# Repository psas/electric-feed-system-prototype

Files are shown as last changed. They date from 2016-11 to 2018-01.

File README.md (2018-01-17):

Electric Feed System
======================

Electric feed system (EFS) aims to design, build, and test an electric feed system prototype using COTS parts and in-house manufacturing for the PSAS LV4 liquid fueled bi-propellant rocket engine by June 6, 2017.

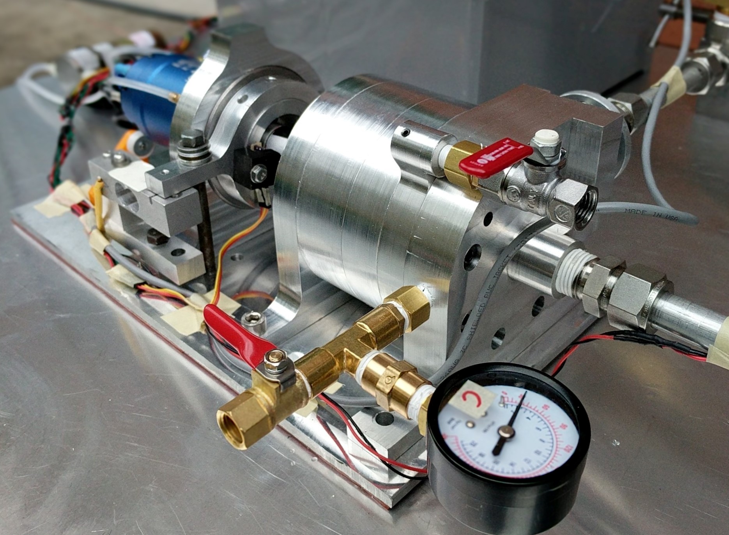
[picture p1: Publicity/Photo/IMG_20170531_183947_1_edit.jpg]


## EFS Requirements:

1. Design and bench test a technology development platform for the electric pump fed system.
2. Design and test a custom power system for EFS motor and system controls.
3. Design for the existing LFE (target chamber pressure of 350 - 400 psi)
4. The pump must be constructed from COTS components.
5. Parallel work with Carbon Fiber Propellant Tank (CFPT) team to optimize vehicle integration.
6. IPython design tool to generate pump requirements based on engine/vehicle level parameters.    
7. Harness the following documentation:
    - EFS testing, handling, and troubleshooting procedures
    - EFS Design Methodology & Design Process
    - Complete bill of materials man

## Stretch Goals:

- Integration with existing Liquid Fuelled Engine Test Stand (LFETS)
- Completed live health monitoring and emergency shutdown provisions
- Cold fire LN2 testing
- Cold fire LOX testing
- Hot  fire LOX testing

### Project Members

Name                | GitHub Username | Current Role
--------------------|-----------------|-----------------------------------
Johnny C. Froehlich | @JordParma      | Team Lead; Design Engineer; Analysis; Testing
James A. Luce       | @luceja         | Mechanical Design Lead; Control Systems
Johnathan Talik     | @jtalik         | Fabrication 
Rawand Rasheed      | @rawand12       | Control Systems
Jordan Roland       | @JSRoland       | Add project role
Mimi Shang          | @mimishang      | Add project role

### Important links

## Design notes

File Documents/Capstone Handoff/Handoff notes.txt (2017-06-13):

Present design:
	Overview of design features
	Individual component analysis
	Subsystems
		Mechanical
		Electrical
		Controls
		Working fluid delivery
	
Design overview questions:

Future work:
	Rework electrical to accomodate more continuous testing
		Power supply?
		Better batteries?
		New motor (custom job?)
	Rework controls for more reliable testing at higher RPM
		Further separation between operators and test stand
		Hide the rats nest somewhere...

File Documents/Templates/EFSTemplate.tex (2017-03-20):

\documentclass[11pt,twoside,a4paper,openright]{report}

\usepackage[utf8]{inputenc}
\usepackage[english]{babel}
\usepackage{lmodern}
\usepackage[T1]{fontenc}
\usepackage{xcolor}
\definecolor{aaublue}{RGB}{33,26,82}
\usepackage{graphicx}
\usepackage{tabularx}
\usepackage{caption}
\captionsetup{%
  font=footnotesize,
  labelfont=bf 
  }
\usepackage{array,booktabs}
\usepackage{wrapfig}
\usepackage{adjustbox}
\usepackage{framed}
\usepackage{amsmath}
\usepackage{amssymb}
\usepackage[framed,amsmath,thmmarks]{ntheorem}
\usepackage{dblfloatfix}
\usepackage{adjustbox}
\usepackage{layouts}

\usepackage[
  left=0.5in,
  right=0.5in,
  bottom=1mm,
  top= 1in,
  ]{geometry}
\usepackage{titlesec}
\titleformat*{\section}{\normalfont\Large\bfseries
    }
\titleformat*{\subsection}{\normalfont\large\bfseries
    }
\titleformat*{\subsubsection}{\normalfont\normalsize\bfseries
    }
%\titleformat*{\paragraph}{\normalfont\normalsize\bfseries}}
%\titleformat*{\subparagraph}{\normalfont\normalsize\bfseries}}

% configure section titles
\usepackage{titlesec}
\titleformat{\section}{\Large\bfseries}{\thesection}{1em}{}
\titleformat{\subsection}{\large\bfseries}{\thesubsection}{1em}{}

\begin{document}
% custom commands
\newcommand{\windef}[1]{\subsection*{\underline{DEF:} \normalsize{#1}}} % definition
\newcommand{\winex}[1]{\subsection*{\underline{EX:} \normalsize{#1}}} % example
\newcommand{\winsec}[1]{\section*{\underline{\textbf{#1}}}} % section
\newcommand{\winres}[1]{\begin{math}\Rightarrow\left\{\begin{matrix}#1\end{matrix}\right.\end{math}\hspace{0.2cm}} % result
\newcommand{\winsys}[1]{\begin{math}\left\{\begin{matrix}#1\end{matrix}\right.\end{math}} % system
\newcommand{\winero}[1]{\begin{math}\xrightarrow{#1}\end{math}} % row operation
\newcommand{\winmat}[1]{\begin{math}\begin{bmatrix}#1\end{bmatrix}\end{math}} % matrix
\newcommand{\winsub}[1]{\subsection*{$\star$\hspace{0.2cm} #1}} % dot
\newcommand{\step}[1]{\begin{math}\xrightarrow{\text{#1}}\end{math}} % step in a process
\newcommand{\winrtwo}{\begin{math}\text{R}^\text{2}\end{math}}
\newcommand{\winrthree}{\begin{math}\text{R}^\text{3}\end{math}}
\newcommand{\wineq}[1]{\begin{equation}\notag#1\end{equation}}
\newcommand{\winans}[1]{\begin{equation}\underline{\underline{\notag\boldsymbol{#1}}}\Leftarrow\end{equation}}
\newcommand{\horrule}[1]{\rule{\linewidth}{#1}} % Create horizontal rule command with 1 argument of height

\begin{titlepage}

\vfil
	\centering
	{\huge\bfseries PSAS Liquid Propellant Rocket Engine
Electric Feed System\par}
	\vspace{0.5cm}
	{\scshape\Large Conceptual Design Progress Report\par}% Insert Document title here

\vspace{2cm}

	{\Large\itshape 	{Jorden Roland, 
John Froehlich,\\
James Luce, 
Mimi Shang,\\
John Talik, 
Rawand Rasheed\par}}

\vspace{3cm}
Faculty advisor:\par
    \textsc{Ra\'{u}l Bayo\'{a}n Cal}\par
	Supervised by:\par
    \textsc{Erin Schmidt}\\
	and\\
	\textsc{Andrew Greenberg}

	\vspace{3cm}
	
%textwidth in cm: \printinunitsof{cm}\prntlen{\textwidth}

\begin{table*}[!t]

  \begin{tabular}{  p{2cm}  m{13.20337cm}  p{2cm}  }
  
\\ \hline

\begin{minipage}{.3\textwidth}
 \begin{flushleft}
      
 \end{flushleft}
\end{minipage}

&

\begin{center}
	{Portland State Aerospace Society}\par
	{Fariborz Maseeh College of Engineering and Computer Science}\par
	{\large \today \par}
	\end{center}

&	

\begin{minipage}{.3\textwidth}
%\begin{flushright}
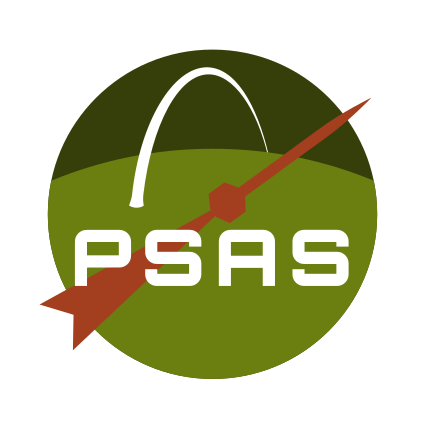
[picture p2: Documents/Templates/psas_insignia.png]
      
%      \end{flushright}
    \end{minipage}\\ \hline
   
\end{tabular}
\end{table*}

\end{titlepage}
\newgeometry{top=10mm,bottom=10mm,right=15mm,left=15mm}
\newpage

\winsec{Nomenclature:}

\centering{
\begin{tabularx}{1.5\textwidth}{c c c c}\par
\textbf{Symbol:} & \textbf{Name:} & \textbf{Formula:} & \textbf{Dependecies:}\par
\end{tabularx}\par
}

\winsec{Abstract:}   %comment out this line and the next if there is no abstract!!!

\newpage
\winsec{Introduction:}
\winsec{Model:}
\winsec{Results:}
\winsec{Conclusion:}
\winsec{Acknowledgments:}
\winsec{References:}

\end{document}

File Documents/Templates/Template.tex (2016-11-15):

\documentclass[12pt]{article}
\usepackage[T1]{fontenc}
\usepackage{graphicx}
\usepackage[font=small]{caption}
\usepackage{amsmath,amssymb,amsfonts,amsthm}
\usepackage{eso-pic}
\usepackage{lastpage}
\usepackage[left=2.7cm,right=1.7cm,top=1.65cm,bottom=1.0cm]{geometry}

\usepackage{fontspec}

\usepackage{tkz-euclide}
\usepackage{multicol}
\usepackage{pgfplots}
\pgfplotsset{compat=1.8}
\usepackage{pgfplotstable}
\usepackage{tikz}
\usetkzobj{all}
\usepackage{booktabs}
\usepackage{listings}
\usepackage{stmaryrd}
%\usepackage{courier}
%\setmonofont{Courier New}
\lstset{
language=R,
basicstyle=\scriptsize\ttfamily,
commentstyle=\ttfamily\color{gray},
numbers=left,
numberstyle=\ttfamily\color{gray}\footnotesize,
stepnumber=1,
numbersep=5pt,
backgroundcolor=\color{white},
showspaces=false,
showstringspaces=false,
showtabs=false,
frame=single,
tabsize=2,
captionpos=b,
breaklines=true,
breakatwhitespace=false,
title=\lstname,
escapeinside={},
keywordstyle={},
morekeywords={},
morecomment=[l][\color{red}]{>\ }
}

% configure page header
\usepackage{fancyhdr}
\setlength{\headheight}{18pt}
\pagestyle{fancy}\fancyhf{}
\renewcommand{\headrulewidth}{0pt}
\renewcommand{\footrulewidth}{0pt}
\lhead{\large{11/3/16}}
\chead{\large{ME 488 - HWK \#004}\hspace{1.4cm}}
\rhead{\large{\MakeUppercase{JORDEN ROLAND}}\hspace{1.5cm}\thepage\hspace{0.1cm}/\hspace{0.1cm}\pageref{LastPage}\hspace{-1.5cm}}

% background image
\newcommand\BackgroundPic{
\put(0,0){
\parbox[b][\paperheight]{\paperwidth}{%
\vfill
\centering
%
\vfill
}}}

% configure section titles
\usepackage{titlesec}
\titleformat{\section}{\Large\bfseries}{\thesection}{1em}{}
\titleformat{\subsection}{\large\bfseries}{\thesubsection}{1em}{}

\begin{document}

\AddToShipoutPicture{\BackgroundPic}

% custom commands
\newcommand{\windef}[1]{\subsection*{\underline{DEF:} \normalsize{#1}}} % definition
\newcommand{\winex}[1]{\subsection*{\underline{EX:} \normalsize{#1}}} % example
\newcommand{\winsec}[1]{\section*{\underline{#1}}} % section
\newcommand{\winres}[1]{\begin{math}\Rightarrow\left\{\begin{matrix}#1\end{matrix}\right.\end{math}\hspace{0.2cm}} % result
\newcommand{\winsys}[1]{\begin{math}\left\{\begin{matrix}#1\end{matrix}\right.\end{math}} % system
\newcommand{\winero}[1]{\begin{math}\xrightarrow{#1}\end{math}} % row operation
\newcommand{\winmat}[1]{\begin{math}\begin{bmatrix}#1\end{bmatrix}\end{math}} % matrix
\newcommand{\winsub}[1]{\subsection*{$\star$\hspace{0.2cm} #1}} % dot
\newcommand{\step}[1]{\begin{math}\xrightarrow{\text{#1}}\end{math}} % step in a process
\newcommand{\winrtwo}{\begin{math}\text{R}^\text{2}\end{math}}
\newcommand{\winrthree}{\begin{math}\text{R}^\text{3}\end{math}}
\newcommand{\wineq}[1]{\begin{equation}\notag#1\end{equation}}
\newcommand{\winans}[1]{\begin{equation}\underline{\underline{\notag\boldsymbol{#1}}}\Leftarrow\end{equation}}
%%%%%%%%%%%%%%%%%%%%%%
% start writing here %
%%%%%%%%%%%%%%%%%%%%%%
\winsec{Question 1: Fractional Factorials}

\winsub{Given}

\begin{enumerate}
  \item $2^{5-2}$
  \item $2^{8-4}$
  \item $2^6$
\end{enumerate}

\winsub{Find}

Runs per replicate needed for each of the above Fractional Factorials

\winsub{Solution}

\begin{enumerate}
  \item $2^{5-2} = 2^3 = 8$ runs per replicate.
  \item $2^{8-4} = 2^4 = 16$ runs per replicate.
  \item $2^6 = 64$ runs per replicate.
\end{enumerate}

\vspace{0.5in}
\noindent\hfil\rule{0.5\textwidth}{.8pt}\hfil

\winsec{Question 2: Use R to Generate Fractional Factorials}

\winsub{Given}

\begin{enumerate}
  \item Any $2^{5-1}$
  \item A $2^{8-3}$ with the generators F=ABC, G=ABD, H=BCD
\end{enumerate}

\winsub{Find}

Use R and the FrF2 Package to create the above and display the +1/-1 matrices

\newpage

\winsub{Solution}
\begin{enumerate}
\item \hspace{1.0cm}\begin{lstlisting}
> library(DoE.base)
> library(FrF2)
> FrF2(2^4,5)
    A  B  C  D  E
1  -1  1  1  1 -1
2   1  1 -1 -1  1
3  -1  1 -1  1  1
4  -1 -1  1  1  1
5   1 -1  1 -1  1
6   1  1  1  1  1
7   1 -1  1  1 -1
8  -1  1 -1 -1 -1
9   1  1 -1  1 -1
10 -1 -1 -1 -1  1
11 -1 -1  1 -1 -1
12  1  1  1 -1 -1
13  1 -1 -1 -1 -1
14 -1 -1 -1  1 -1
15 -1  1  1 -1  1
16  1 -1 -1  1  1
class=design, type= FrF2 
\end{lstlisting}
\item  \hspace{1.0cm}\begin{lstlisting}
> FrF2(2^5,8,generator=c("ABC","ABD","BCD"))
    A  B  C  D  E  F  G  H
1   1 -1 -1  1  1  1 -1  1
2  -1 -1 -1  1  1 -1  1  1
3  -1  1  1  1 -1 -1 -1  1
4   1  1  1  1  1  1  1  1
5  -1 -1  1  1  1  1  1 -1
6   1  1 -1  1  1 -1  1 -1
7   1 -1  1  1  1 -1 -1 -1
8  -1 -1  1 -1  1  1 -1  1
9  -1  1 -1  1 -1  1 -1 -1
10 -1  1  1 -1  1 -1  1 -1
11  1 -1  1 -1  1 -1  1  1
12 -1  1 -1 -1  1  1  1  1
13  1 -1 -1 -1  1  1  1 -1
14  1  1 -1  1 -1 -1  1 -1
15 -1  1 -1 -1 -1  1  1  1
16 -1 -1 -1  1 -1 -1  1  1
17 -1  1  1  1  1 -1 -1  1
18 -1 -1 -1 -1  1 -1 -1 -1
19  1 -1 -1  1 -1  1 -1  1
20  1 -1 -1 -1 -1  1  1 -1
21  1 -1  1 -1 -1 -1  1  1
22  1  1 -1 -1  1 -1 -1  1
23  1  1  1  1 -1  1  1  1
24 -1 -1  1 -1 -1  1 -1  1
25  1  1  1 -1 -1  1 -1 -1
26 -1  1  1 -1 -1 -1  1 -1
27  1 -1  1  1 -1 -1 -1 -1
28 -1 -1 -1 -1 -1 -1 -1 -1
29 -1 -1  1  1 -1  1  1 -1
30  1  1 -1 -1 -1 -1 -1  1
31 -1  1 -1  1  1  1 -1 -1
32  1  1  1 -1  1  1 -1 -1
class=design, type= FrF2.generators
\end{lstlisting}
\end{enumerate}

\newpage

\winsec{Question 3: Aliasing}

\winsub{Given}

\begin{enumerate}
  \item I=ABCD=EBCD=AE
  \item I=ABCDE
\end{enumerate}

\winsub{Find}

The aliases of 'BC' in each of the above

\winsub{Solution}

\begin{enumerate}
  \item Multiply through the defining words by `BC' gives its aliases.\\
  (BC)I=(BC)ABCD=(BC)EBCD=(BC)AE $\shortrightarrow$  BC=AD=ED=ABCE
  \item Repeat step above.\\
  (BC)I=(BC)ABCDE $\shortrightarrow$ BC=ADE
  \end{enumerate}

\vspace{0.5in}
\noindent\hfil\rule{0.5\textwidth}{.8pt}\hfil

\winsec{Question 4: Resolution}

\winsub{Find}

Explain why a $R_{II}$ fractional experiment is a bad idea? Use an example to illustrate your point.

\winsub{Solution}
In general a $R_{II}$ fractional experiment is not particularly useful because main effects will be confounded with other main effects making it unclear which of the factors is causing a change in the resonse.\\

EX: The simplest case is a $2^{2-1}$ experiment with defining relationship I=AB. In this case A=B and B=A making the two factors being tested completely indistiguishable from each other.

\newpage

\winsec{Question 5: Concepts of Half Fractional}

\winsub{Given}

$2^{4-1}$ Half Fractional Factorial Experiment with the D=ABC generator

\winsub{Find}

The process to create the 'other' half. Hint: D=ABC means D=+ABC

\winsub{Solution}
Generating the ``other half'' of the experiment simply requires setting D=-ABC as below.
\begin{lstlisting}
> FrF2(2^3,4,generator=c("-ABC"))
   A  B  C  D
1  1  1  1 -1
2 -1  1  1  1
3 -1 -1 -1  1
4  1 -1  1  1
5  1 -1 -1 -1
6  1  1 -1  1
7 -1 -1  1 -1
8 -1  1 -1 -1
class=design, type= FrF2.generators 
\end{lstlisting}

\newpage
\winsec{Question 6: Application}

\winsub{Given}

You have been given authorization to study a flame-resistant material. There are 8 key factors, (A,B,C,D,E,F,G,H)

\winsub{Find}

\begin{enumerate}
  \item How many samples at a minimum would you need to request to perform a Full Fractional Experiment of any use?
  \item You have been authorized only 100 samples at maximum. What are the feasible Balanced Fractional Experiments you could run?
  \item For each of the experiments you listed in the last part, what are the engineering trade-offs in the feasible ones?
  \item Pick your choice of experiment and state issues with that experiment you would need to keep in consideration during the analysis phase.
  \item Assume DE and BC are significant and critical two way interactions, use the FrF2 package to determine generators for your choice above to address these.
\end{enumerate}

\winsub{Solution}

\begin{enumerate}
  \item $2^8=256$ runs per replicate. Assuming at \textbf{least} 2 runs for a reasonable number of $df_{error}$ gives $256*2=512$ samples.
  
  \item \textbf{Half-fractional:}	$2^{8-1}=128$ still too many samples.\\
  \textbf{Quarter-fractional:}   $2^{8-2}=64$ This is a pretty good option. ($R_{V}$) and less than 100 samples.\\
  \textbf{Eighth-fractional:} $2^{8-3}=32$ This is probably a low number of samples but not a terrible option ($R_{IV}$). Also leaves enough room to run a second and third replicate which is never bad.\\
  \textbf{Sixteenth-fractional:} $2^{8-4}=16$ Still $R_{IV}$  so this is not a bad option really, allows for oportunity to run multiple replicates. However there may be significant 2-way interactions which are aliased.
  
  \item See above.
  \item Choosing the Eighth-fractional design gives the best options for aliasing combined with the above stated 3 replicates within the funding allowance means that this is likely the best design.
  
  \newpage

  \item Using the FrF2 function in R with the following generators: F=ABC, G=ABD, H=BCDE
  \begin{lstlisting}
  > design.info(FrF2(2^5,8,generator=c("ABC","ABD","BCDE")))$aliased
$legend
[1] "A=A" "B=B" "C=C" "D=D" "E=E" "F=F" "G=G" "H=H"
$main
character(0)
$fi2
[1] "AB=CF=DG" "AC=BF"    "AD=BG"    "AF=BC"    "AG=BD"    "CD=FG"    "CG=DF" 
  \end{lstlisting}
  As shown above DE and BC are not aliased with other interactions and mains are not confounded. this is a solid design.
  
\end{enumerate}

\noindent\hfil\rule{0.5\textwidth}{.8pt}\hfil
\begin{center}
  \textbf{END OF ASSIGNMENT}
\end{center}
\end{document}

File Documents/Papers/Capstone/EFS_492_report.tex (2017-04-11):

\documentclass[11pt,twoside,a4paper,openright]{report}

\usepackage[utf8]{inputenc}
\usepackage[english]{babel}
\usepackage{lmodern}
\usepackage[T1]{fontenc}
\usepackage[table]{xcolor}
\definecolor{aaublue}{RGB}{33,26,82}
\usepackage{graphicx}
\usepackage{tabularx}
\usepackage{caption}
\captionsetup{%
  font=footnotesize,
  labelfont=bf 
  }
\usepackage{array,booktabs}
\usepackage{wrapfig}
\usepackage{adjustbox}
\usepackage{framed}
\usepackage{amsmath}
\usepackage{amssymb}
\usepackage[framed,amsmath,thmmarks]{ntheorem}
\usepackage{dblfloatfix}
\usepackage{adjustbox}
\usepackage{layouts}
\usepackage{lipsum}
\usepackage{pdfpages}
\usepackage{verbatim}
\usepackage{rotating}

\usepackage[
  left=0.5in,
  right=0.5in,
  bottom=1mm,
  top= 1in,
  ]{geometry}
\usepackage{titlesec}
\titleformat*{\section}{\normalfont\Large\bfseries
    }
\titleformat*{\subsection}{\normalfont\large\bfseries
    }
\titleformat*{\subsubsection}{\normalfont\normalsize\bfseries
    }
%\titleformat*{\paragraph}{\normalfont\normalsize\bfseries}}
%\titleformat*{\subparagraph}{\normalfont\normalsize\bfseries}}

% configure section titles
\usepackage{titlesec}
\titleformat{\section}{\Large\bfseries}{\thesection}{1em}{}
\titleformat{\subsection}{\large\bfseries}{\thesubsection}{1em}{}

\begin{document}
% custom commands
\newcommand{\windef}[1]{\subsection*{\underline{DEF:} \normalsize{#1}}} % definition
\newcommand{\winex}[1]{\subsection*{\underline{EX:} \normalsize{#1}}} % example
\newcommand{\winsec}[2]{\section*{\underline{\textbf{#1}}{#2}}} % section
\newcommand{\winres}[1]{\begin{math}\Rightarrow\left\{\begin{matrix}#1\end{matrix}\right.\end{math}\hspace{0.2cm}} % result
\newcommand{\winsys}[1]{\begin{math}\left\{\begin{matrix}#1\end{matrix}\right.\end{math}} % system
\newcommand{\winero}[1]{\begin{math}\xrightarrow{#1}\end{math}} % row operation
\newcommand{\winmat}[1]{\begin{math}\begin{bmatrix}#1\end{bmatrix}\end{math}} % matrix
\newcommand{\winsub}[1]{\subsection*{\hspace{0.2cm}\textit{ #1}}} % dot
\newcommand{\step}[1]{\begin{math}\xrightarrow{\text{#1}}\end{math}} % step in a process
\newcommand{\winrtwo}{\begin{math}\text{R}^\text{2}\end{math}}
\newcommand{\winrthree}{\begin{math}\text{R}^\text{3}\end{math}}
\newcommand{\wineq}[1]{\begin{equation}\notag#1\end{equation}}
\newcommand{\winans}[1]{\begin{equation}\underline{\underline{\notag\boldsymbol{#1}}}\Leftarrow\end{equation}}
\newcommand{\horrule}[1]{\rule{\linewidth}{#1}} % Create horizontal rule command with 1 argument of height

\begin{comment}
\begin{titlepage}

\vfil
	\centering
	{\huge\bfseries PSAS Liquid Propellant Rocket Engine
Electric Feed System\par}
	\vspace{0.5cm}
	{\scshape\Large Conceptual Design Progress Report\par}% Insert Document title here

\vspace{5cm}

	{\Large\itshape 	{Jorden Roland, 
John Froehlich,\\
James Luce, 
Mimi Shang,\\
John Talik, 
Rawand Rasheed\par}}

\vspace{3cm}
Faculty advisor:\par
    \textsc{Ra\'{u}l Bayo\'{a}n Cal}\par
	Supervised by:\par
    \textsc{Erin Schmidt}\\
	and\\
	\textsc{Andrew Greenberg}

	\vspace{3cm}
	
%textwidth in cm: \printinunitsof{cm}\prntlen{\textwidth}

\begin{table*}[!t]

  \begin{tabular}{  p{2cm}  m{13.20337cm}  p{2cm}  }
  
\\ \hline

\begin{minipage}{.3\textwidth}
 \begin{flushleft}
      
 \end{flushleft}
\end{minipage}

&

\begin{center}
	{Portland State Aerospace Society}\par
	{Fariborz Maseeh College of Engineering and Computer Science}\par
	{\large \today \par}
	\end{center}

&	

\begin{minipage}{.3\textwidth}
%\begin{flushright}
      
%      \end{flushright}
    \end{minipage}\\ \hline
   
\end{tabular}
\end{table*}

\end{titlepage}
\newgeometry{top=1in,bottom=1in,right=1in,left=1in}
\newpage
\thispagestyle{empty}

\winsec{Executive Summary: }{}
\vspace{12pt}
The Electric Feed System (EFS) team will design, build, and test an electric feed system prototype to serve as a technology development platform for the PSAS LV4 rocket using commercial off the shelf (COTS) parts and in-house manufacturing by June 16, 2017 and for less than \$15,800.\par
\vspace{12pt}
As of the time of this report, the EFS project is developing the first prototype, which will use water as its working fluid, and is transitioning from design to fabrication and testing. The project is currently ahead of the milestone schedule established by the project plan. \par
\vspace{12pt}
Efforts over the last two months have largely focused on pump sizing and impeller design. The critical decision has been made to transition from theory to validation through physical experiment, allowing us to proceed with the first prototype test. Along with pump theory and design, there have been ongoing parallel efforts to complete the other tasks required for the first prototype test, such as development of controls and data acquisition systems, sensor calibration, completion of CAD design, and identification and acquisition of critical components such as a motor, speed controller, and battery.\par
\vspace{12pt}
Our next milestone is the finalization of detailed design, encompassing impeller design, COTS parts selection, system simulation, and CAD modeling for the first prototype, planned for 3/26/17 but nearly complete as of 3/17/17. The associated milestone of finishing COTS part purchasing, due 4/2/17, is also largely complete and should be finished by 3/24/17.\par
\vspace{12pt}
The two critical following milestones are the assembly and testing of the first prototype, originally planned for 4/24/17 and 5/6/17, respectively. These two steps are now anticipated to be completed by 3/31/17 and 4/7/17, as much of the work required to execute this first test is either complete, underway, or well planned for. The major tasks preceding the first prototype test will be fabrication of the pump assembly, procurement of miscellaneous remaining COTS parts, and assembly of the test apparatus.\par
\vspace{12pt}
Looking forward to the final deliverable of a tested second prototype using liquid oxygen as a working fluid, our current status encourages us that we will be able to confront the challenges exposed by physical testing and the development of the final prototype.\par
\vspace{4cm}

\begin{flushright}
\begin{tabular}[t]{@{}p{3.5in}@{}}
  \\[-2ex]
  \strut \textit{Signature: }\underline{\hspace{2.75in}}\strut
  \end{tabular}\\
  {Ra\'{u}l Bayo\'{a}n Cal}\\
Faculty advisor
\end{flushright}

\newpage

%\includepdf{Summary_efs.pdf} <------This doesnt work for some reason.

\setcounter{page}{1}
\winsec{Conceptual Design Summary: }{}
\vspace{12pt}
The EFS project was provided to the team with most of the conceptual design decisions wrapped up in the engine/vehicle level requirements. The majority of complex decisions involving trade offs are occurring at an analytical level in the pump sizing process. For the EFS project, descisions regarding different propulsion types, such as solid motors, pressure fed liquid, or liquid turbopump engines have already been made. The EFS will use electric motor driven centrifugal pumps, powered by a lithium polymer batteries, using liquid oxygen (oxidizer) and isopropyl alcohol (fuel) as propellants, given a specific inlet pressure and producing a required flow rate and pressure head. Thus, for the EFS team, the highest level decisions were subsystem component level decisions, including choosing an impeller type and impeller housing design.\par
\vspace{12pt}
\winsub{Concept selection process: Impeller type}
\vspace{12pt}
For conventional pump design, the choice of impeller type would be a straightforward output of a pump sizing process and would not represent a major concept selection. The nature of the EFS project required a deeper investigation into impeller style, as the consequences this selection affects nearly all other subsystems. Typically, pump sizing calculations use a set of requirements to  produce a specific speed value, and impeller style is dictated by this value which dictates an impeller style. For example, a particular specific speed value might imply that a Francis vane impeller is more ideal than a normal radial vane impeller, see figure 1 below. The EFS project’s requirements specify an unusually high head and low flow rate, resulting in a specific speed requirement that falls outside of the ranges of common impeller types. \par
	
\begin{figure}[h]
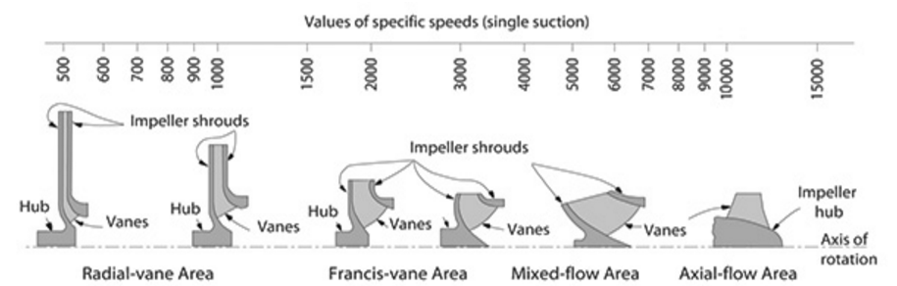
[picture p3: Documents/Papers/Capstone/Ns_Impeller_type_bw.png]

\caption{Typical flow classification of pump impellers as per specific speed}
\end{figure}

\vspace{12pt}
This forced a radical departure from the typical options found in pump design documentation. Literature review outside of the normal canon of rocket pump design led to the exploration of a Barske design impeller: an unorthodox, straight vane radial impeller design suitable for low flow, high head, and low specific speed requirements.\par
\vspace{12pt}
The decision was made to proceed with designing the EFS system around a Barske impeller for two reasons: a Barske design is suitable for our pump’s specific speed range and it is easier to manufacture than more geometrically complex impellers. The downside of the Barske design is that it is not represented well in the common pump sizing documentation, and thus may require more experimental testing to characterize its performance. In our application, this is 
\newpage
\noindent
not necessarily a loss. As the performance requirements of the EFS largely fall outside of the regimes covered by common pump sizing documentation already, and thorough experimentation will be required for any approach. In other words, the unknown characteristics of Barske impellers is not a high risk, as the EFS' requirements put the impeller outside of common pump characteristics. Consequently, there was no perceived trade-off in the decision to proceed with a Barske impeller. A subsystem performance matrix interpreting this decision is included in the appendix.\par

\vspace{12pt}
%--------------------------------------------------------------------------------------------------------------------------%
%--------------------------------------------------begin screening matrix---------------------------------------------%
%--------------------------------------------------------------------------------------------------------------------------%
\begin{table*}[!h]
\caption{Screening matrix for impeller design choice}
\resizebox{\textwidth}{!}{%
\begin{tabular}{|c||c|c|c|}
\hline
                          &{Specific speed range} &{Manufacturability}&{Testing requirements}  \\ 
                          &{($<500$ is required)}&                           &                                    \\ \hline \hline
Common designs  &  & Very complex: investment casting & Designs are included \par  \\
(radial, Francis, mixed flow, axial) &500-8000 (too high)&or 5 axis milling of impeller and housing.&in pump sizing literature but requirements fall \\
&&&outside of common regimes.\\ \hline
Barske design &400-1000 (appropriate)&Very simple: impeller and housing&Not included in common literature and\\
&& can be made with 3 axis mill.&experimentation required to characterize.\\ \hline
\end{tabular}}

\end{table*}
%----------------------------------------------------------------------------------------------------------------------------%

\winsub{Concept selection process: Housing type}
\vspace{12pt}
Another major decision was to determine the housing type to be used for the initial prototype and water testing. A simple option for an impeller housing is a concentric design, which is the easiest to manufacture but may reduce efficiency and performance. Higher performance housing options might include an expanding volute or the addition of a cutwater to the concentric design. Figure 2 shows two potential options for housing design.\par

\vspace{12pt}
\begin{figure}[h]
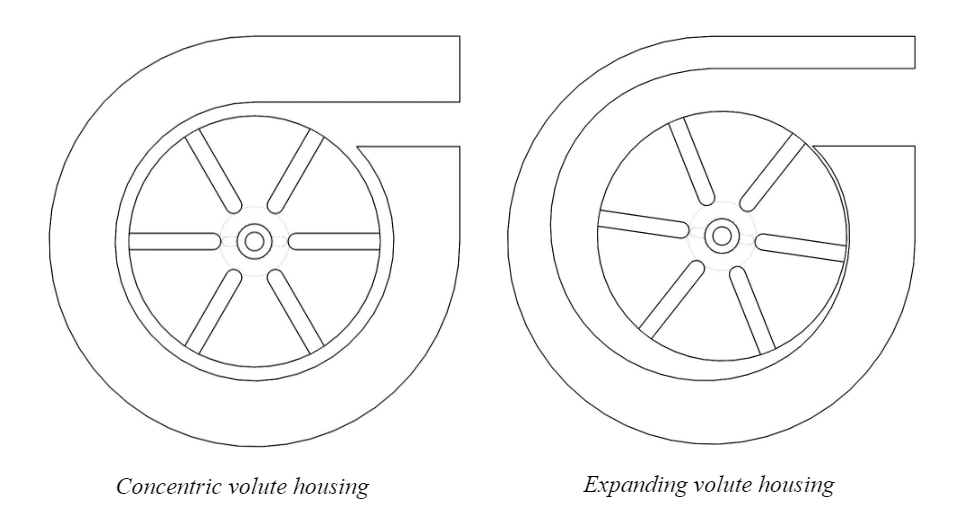
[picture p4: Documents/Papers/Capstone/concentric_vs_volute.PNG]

\caption{Example of a concentric bowl design versus a non-concentric volute design}
\end{figure}

\newpage
The final product of the EFS project has high performance requirements that may require use of performance enhancing techniques, such as housing modifications like an expanding volute. The goal of the first prototype is to provide theory validation, not hit final performance targets, and thus has a unique set of requirements that differ from the second prototype's. For example, although the final prototype needs to achieve 350 psi at 11 gpm flow, the first prototype's true goal is to achieve performance in a range such that we can calibrate the assumptions in our theory to design the second prototype accordingly. \par
\vspace{12pt}
This difference in utility between the two prototype dictates the choice of housing type for the first prototype. While there is a benefit to seeing higher performance in the first prototype, there is the cost to having additional variables to consider when interpreting the first prototype test data. The first prototype test is intended to isolate the influence of factors represented in the pump sizing theory we are using for our fundamental design calculations. For example, impeller diameter, height, blade number, inlet size, and outlet size are critical dependent variables. Conveniently, many of these variables are connected, and a test regimen does not need to independently manipulate each variable. Introducing housing design as a dependent variable at this stage would dramatically complicates the testing required without providing clear validation of the theory used in the design.\par
\vspace{12pt}
%--------------------------------------------------------------------------------------------------------------------------%
%--------------------------------------------------begin screening matrix---------------------------------------------%
%--------------------------------------------------------------------------------------------------------------------------%
\begin{table*}[!h]
\caption{Screening matrix for housing type selection}
\resizebox{\textwidth}{!}{%
\begin{tabular}{|c||c|c|c|}
\hline
                                              &{Testing influence} &{Performance}&{Costs}  \\ \hline \hline
                                               &  May need to be designed and                            &&Significant design process.\\
Housing with expanding volute,  &  tested for second prototype anyway.                  & May bring us closer to target values. &Cannot be manufactured on lathe.\\
 cutwater, or other modifications & Introduces a unique variable to testing                &&\\
                                               & not represented in our pump sizing calculations.   &&\\ \hline
Concentric housing                    & Simplifies analysis of test data.                           & May cause low performance that&Simple to design.\\
                                               &   & complicates test data analysis.& Can be manufactured on lathe or 3 axis mill.\\ \hline
\end{tabular}}

\end{table*}
%----------------------------------------------------------------------------------------------------------------------------%
\winsub{Concept selection process: Impeller test design}
\vspace{12pt}
The most complex and consequential decision making in this project has involved the design of the impeller. A Python notebook is used to bring together equations incorporating performance requirements, fluid properties and geometric constraints to produce suggestions about impeller dimensions. Trade-offs here are complex. A change in RPM might benefit from a higher blade count which might introduce losses due to narrow fluid channels, while a lower blade count may induce pressure fluctuations, etc.\par
\vspace{12pt}
Given that our application is near the limit of pump sizing regimes, there is significant uncertainty in the design process. For the first prototype, the goal is to produce a set of possible impeller geometries that allow isolation of some of these significant unknowns. Performing experimental runs with combinations of impeller diameter, blade number, and blade tip height will allow a better understanding of pump theory, Barske design behavior, and the hydrodynamic regime that the EFS exists in (Figure 4). The variations of impeller and housing geometries are passed to parameterized CAD drawings designed for machinability (Figure 3). Additionally, the blade geometries are checked  for strength concerns using static finite element analysis.\par

\vspace{12pt}
\begin{figure}[!h]
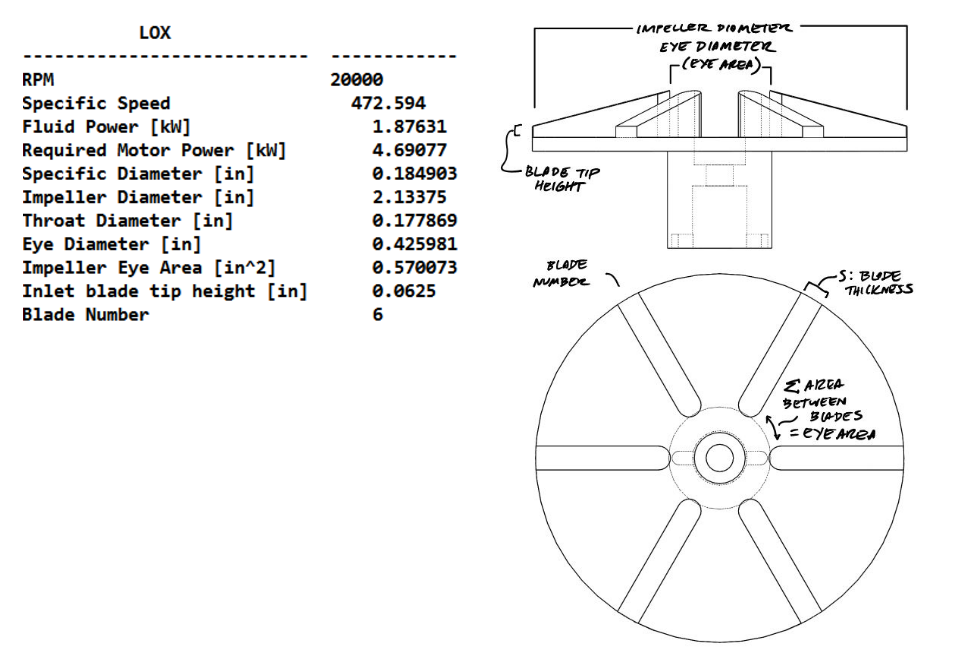
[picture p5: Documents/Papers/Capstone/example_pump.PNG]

\caption{Example outputs from pump sizing python notebook and parameterized CAD impeller drawing output}
\end{figure}

\vspace{12pt}
\begin{figure}[!h]
\begin{centering}
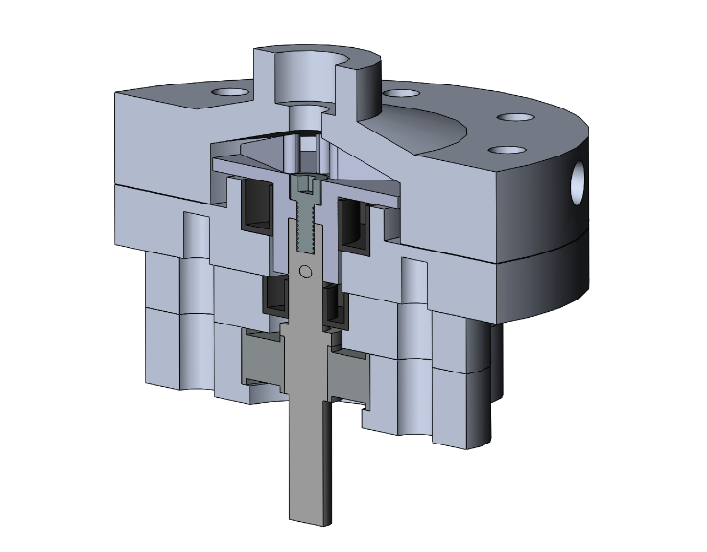
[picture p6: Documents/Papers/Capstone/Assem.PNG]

\caption{Example parameterized CAD pump assembly}
\end{centering}
\end{figure}
\newpage

\winsec{Subsystem decomposition: }{}
\vspace{12pt}
The EFS is comprised of four subsystems: the electric motor system , the controls and data acquisition system, the test stand, and the pump itself. \par
\vspace{12pt}
	The electric motor system is comprised of an electric motor, a battery, and an electronic speed controller (ESC). The data acquisition and controls system uses a Labview-Arduino interface to monitor the pump via pressure and temperature sensors and controls the system through solenoid valves and by directly controlling the motor’s speed controller. The test apparatus system is comprised of propellant and pressurant tanks and provides the propellant to the pump at a specified pressure. The pump itself is the center of the system, with the impeller being the core of the pump subsystem. The impeller may also be considered as a subsystem itself, as the requirements of the impeller dictate the requirements of the rest of the pump system components, including the housing, shaft, and bearings.\par
\vspace{12pt}
	
\begin{figure}[h]
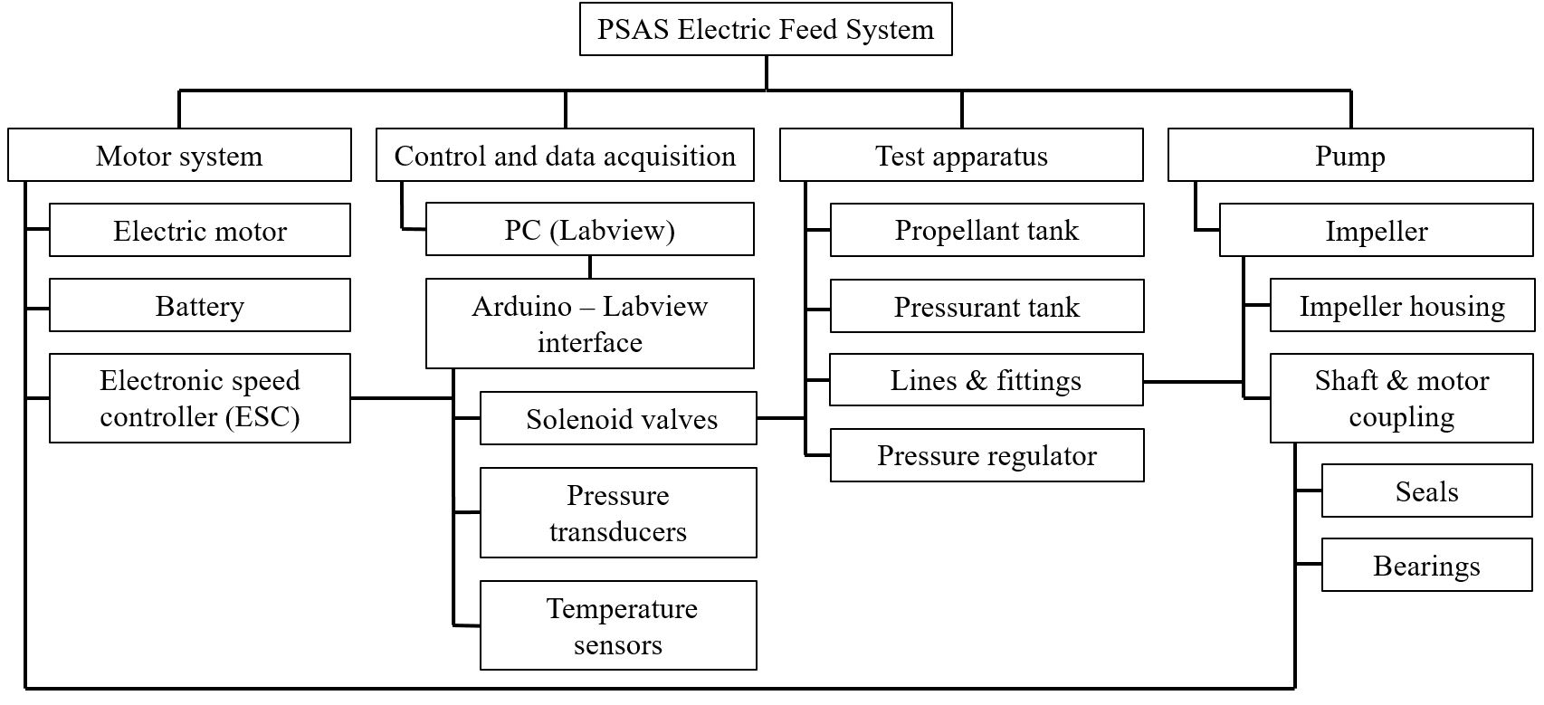
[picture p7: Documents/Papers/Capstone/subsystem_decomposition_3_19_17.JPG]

\caption{Electric feed system hierarchical subsystem decomposition}
\end{figure}

	The motor system connects to the pump subsystem via a coupled shaft that joins the electric motor and the impeller, and the ESC is directly controlled by the Labview-Arduino interface of the controls system. The controls system bridges to the test apparatus by controlling the solenoid valves on the propellant and pressurant tanks, which feed the pump itself.\par

\begin{figure}[h]
\begin{center}
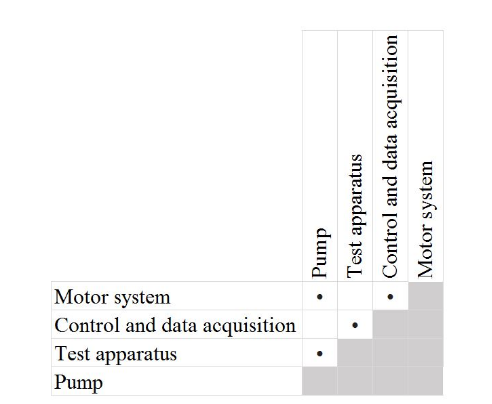
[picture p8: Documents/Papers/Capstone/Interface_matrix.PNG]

\caption{Subsystem interface matrix for the EFS}
\end{center}
\end{figure}

\winsec{Updates on Performance Measures: }{}
\winsub{Key system level performance measures}
The performance measures for the final prototype have remained constant as were provided in the project contract:\par

\begin{itemize}
\item The EFS pumps liquid isopropyl alcohol (IPA) at 1.3-1.4 lbm/s.
\item The EFS pumps liquid oxygen (LOX) at 1.6-1.8 lbm/s.
\item The EFS delivers a discharge pressure greater than 350 psi.
\item The EFS delivers a stable discharge pressure varying less than 10\%.
\item The EFS can sustain operational requirements for 20 seconds.
\item Prototype approximates a flight ready system in terms of mass (less than 10 kg).
\item The pump can be disassembled, moved, and assembled by 3 team members in under 1 hour. 
\end{itemize}

While these final prototype performance measures have not changed, the need for an independent set of requirements unique to the first prototype has become apparent. The first prototype’s intention is to provide feedback for the validation of our pump design theory and calculations, and until the project transitions to the development of the second prototype, the team is functioning under a temporary set of performance measurements unique to that objective:\par

\begin{itemize}
\item The first prototype achieves pressure, flow rate magnitude and stability within +/- 25\% of the final performance measure values. 
\item The first prototype includes a set of experimental impellers and housing variants sufficient to corroborate theory and optimize the second prototype design.
\item The first prototype can record inlet and outlet pressure, RPM and flow rate data at a resolution sufficient to allow accurate data analysis.
\item The first prototype can vary impeller RPM between 10,000 and 50,000 RPM
\item The first prototype can withstand discharge pressures up to 500 psi.
\item The first prototype can sustain operational requirements for 60 seconds.
\item The first prototype can be disassembled, moved, and assembled by 3 team members in under 1 hour. 
\item The first prototype impeller and impeller housing can be changed in under five minutes.
\item The first prototype pump water.
\end{itemize}

	These performance measurements represent the requirements of a test apparatus. The core pump performance metrics are not critical as long as they fall into a range that can be used to refine our pump design theory and calculations. If the first prototype could achieve > \textasciitilde250 psi, we could likely adapt our design to achieve the performance measurements required in the second prototype. Additional measurements unique to the first prototype test involve more rigorous data collection specifications, longer operational duration requirements, and a design accommodation for  easily interchangeable impellers and housings.\par
\vspace{12pt}
	Please note the 1st and 2nd prototype RM matrices for the pump subsystem included in the appendix. The goal of these competing matrices is to clarify that the first prototype has lax pump performance requirements but more stringent testing requirements. The second prototype’s priorities are more focused on the pump performance numbers.\par
\newpage

\winsub{Test plan for verifying performance}
\vspace{12pt}

\begin{table*}[!h]
\caption{Test platform control system}
\resizebox{\textwidth}{!}{%
\begin{tabular}{|c|cr|c|}
\hline
\textbf{Device: }&\textbf{Function: }&&\textbf{Control type: } \\ \hline \hline
Electric motor&&drive the propellant pumps&Electronic \\ \hline
Oxydizer main valve&& Open and close the main oxydizer line&Electronic \\ \hline
Fuel main valve&& Open and close the main fuel line& Electronic \\ \hline
Check valves&& Avoid pump overpressures&Automatic \\ \hline
Tank drain valves&& Evacuate the remaining propellants after burnout or in emergency shutoff&Electronic \\ \hline
Tank fill valves&&Fill tanks before testing& Manual \\ \hline
Pressurization valve&& Pressurizes propellant just before test start& Manual\\ \hline
\end{tabular}}
\end{table*}

\begin{table*}[!h]
\caption{Test performance measurement methods}
\resizebox{\textwidth}{!}{%
\begin{tabular}{|c|cr|cr|}
\hline
\textbf{Variable: }&\textbf{Monitoring device: }&&\textbf{Observations}&\\ \hline \hline
Combustion chamber pressure&&Pressure transducer&&Optionally an indirect method may be used \\ \hline
Injector head inlet pressure&&Pressure transducer&&Absolute pressure type with transducer \\ \hline
Propellants tank pressure&&Indirect measure&&Via gas tank pressure regulator working pressure \\ \hline
Pump rotational speed&&Tachometer&&coupled to motor shaft \\ \hline
Pump Torque&&Dynamometer&& Made using strain gauges\\ \hline
Required electrical power&&Indirect measure&&Sensing simultaneously motor current and voltage \\ \hline
Propellants flow rate&&Indirect measure&&Via pump flow characterization and motor speed sensing \\ \hline
\end{tabular}}
\end{table*}

\winsec{Planning Update: }{}
\vspace{12pt}
The EFS project is currently ahead of the milestone schedule anticipated in our 2/14/17 project plan, particularly for milestones involving the first water pumping prototype. First prototype testing was initially planned by 5/6/17 with data analysis completed by 5/22/17, but those milestones are currently expected to be completed three to four weeks early. This is unlikely to affect milestones involving the second, liquid oxygen pumping prototype, as the results of the first prototype test will determine whether additional design-test iteration of the first prototype will be needed to validate our theory and design before proceeding with the more challenging, liquid oxygen pumping second prototype. Being ahead of schedule is small relief given the daunting challenges of the final prototype’s requirements. Please see the updated Gantt chart in the appendix.\par

\end{comment}
\newpage
\pagenumbering{Roman}
\winsec{Appendix A1:}{ Updated Gantt Chart}
%---------------------------------%
%New Gantt Chart Goes here!%
%---------------------------------%

\begin{center}
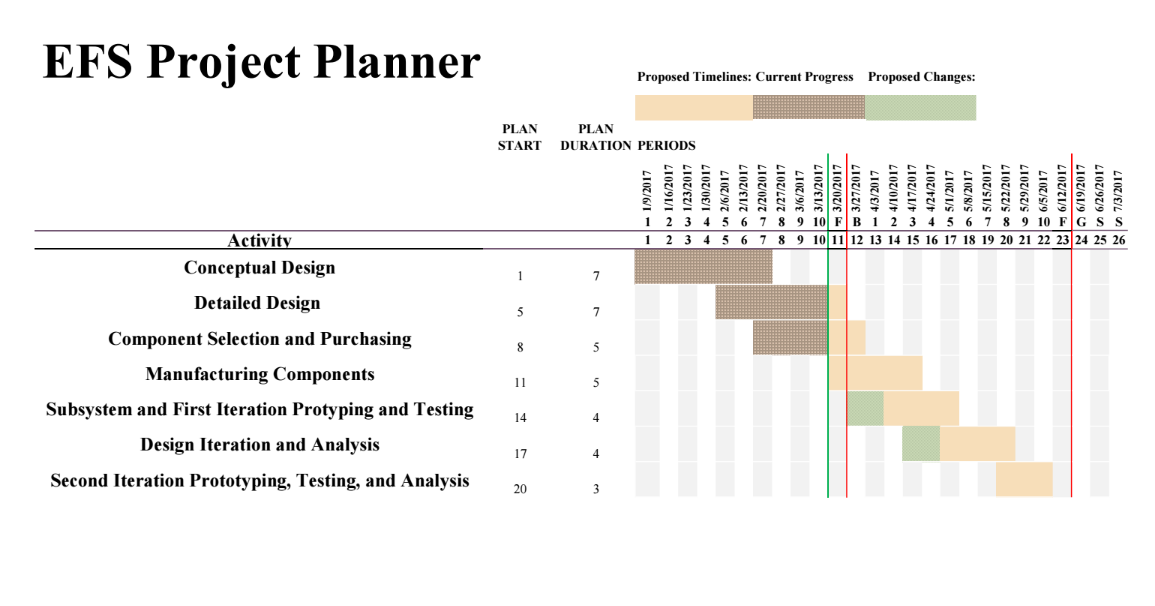
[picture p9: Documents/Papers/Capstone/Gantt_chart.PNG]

\end{center}

\winsec{Appendix A2:}{ Requirements and Measurements Matrix}
%---------------------------------%
% New RM matrix Goes here! %
%---------------------------------%

\setcounter{figure}{0} \renewcommand{\thefigure}{A.\arabic{figure}}

\begin{figure}[!h]
\begin{center}
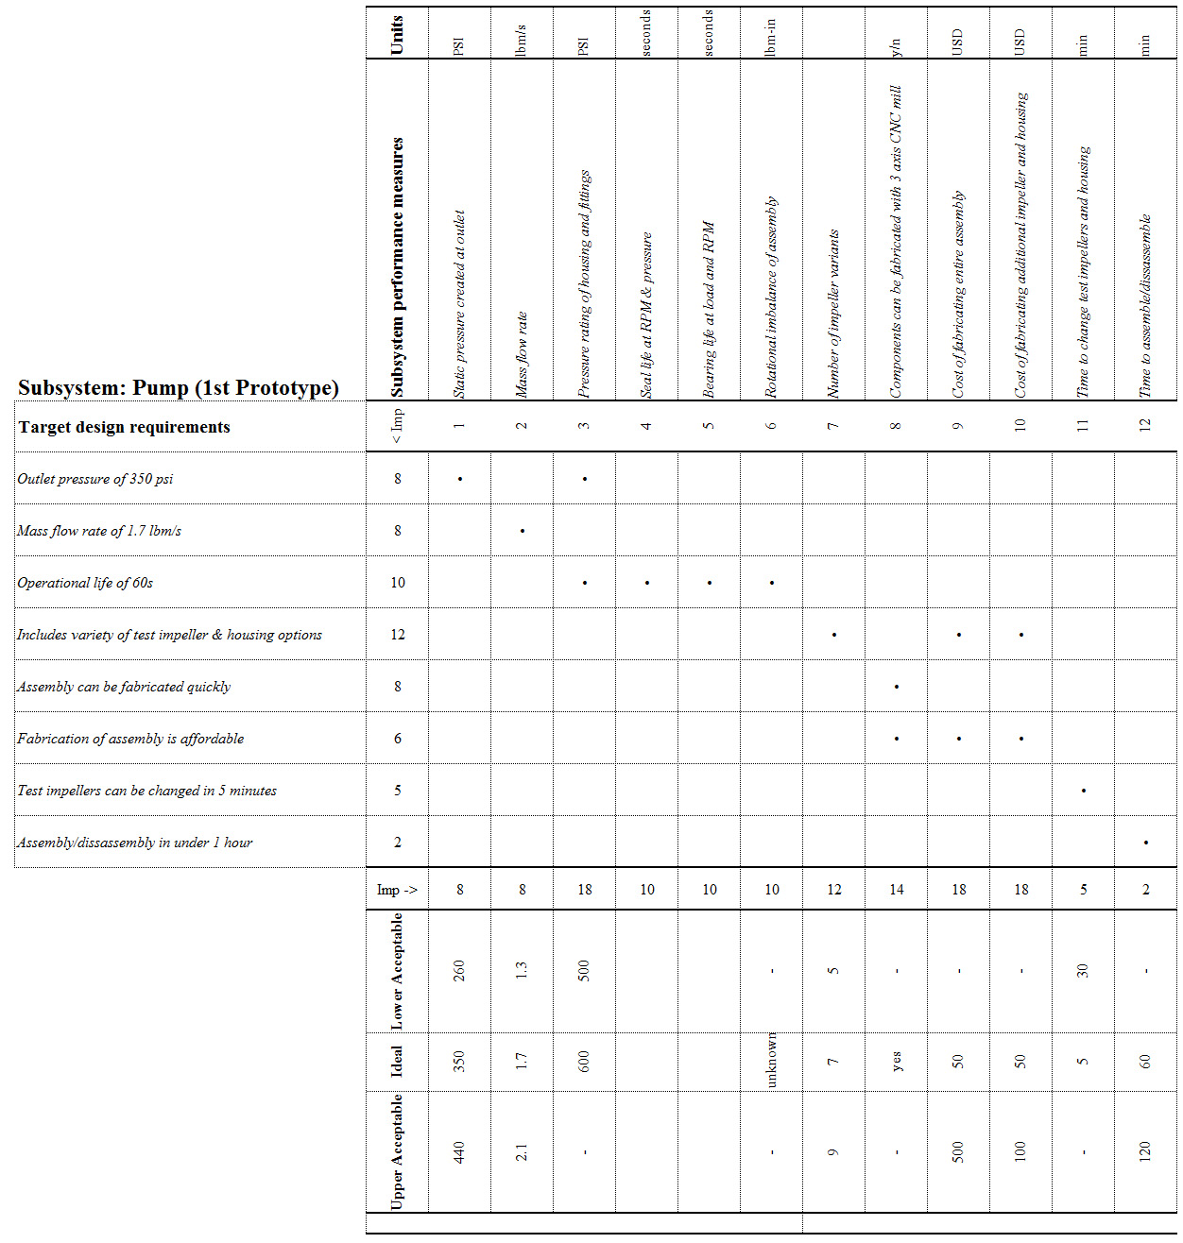
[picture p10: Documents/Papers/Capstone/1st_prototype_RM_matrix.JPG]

\caption{Requirements/measurements matrix for the first prototype EFS}
\end{center}
\end{figure}
\newpage
\begin{figure}[!h]
\begin{center}
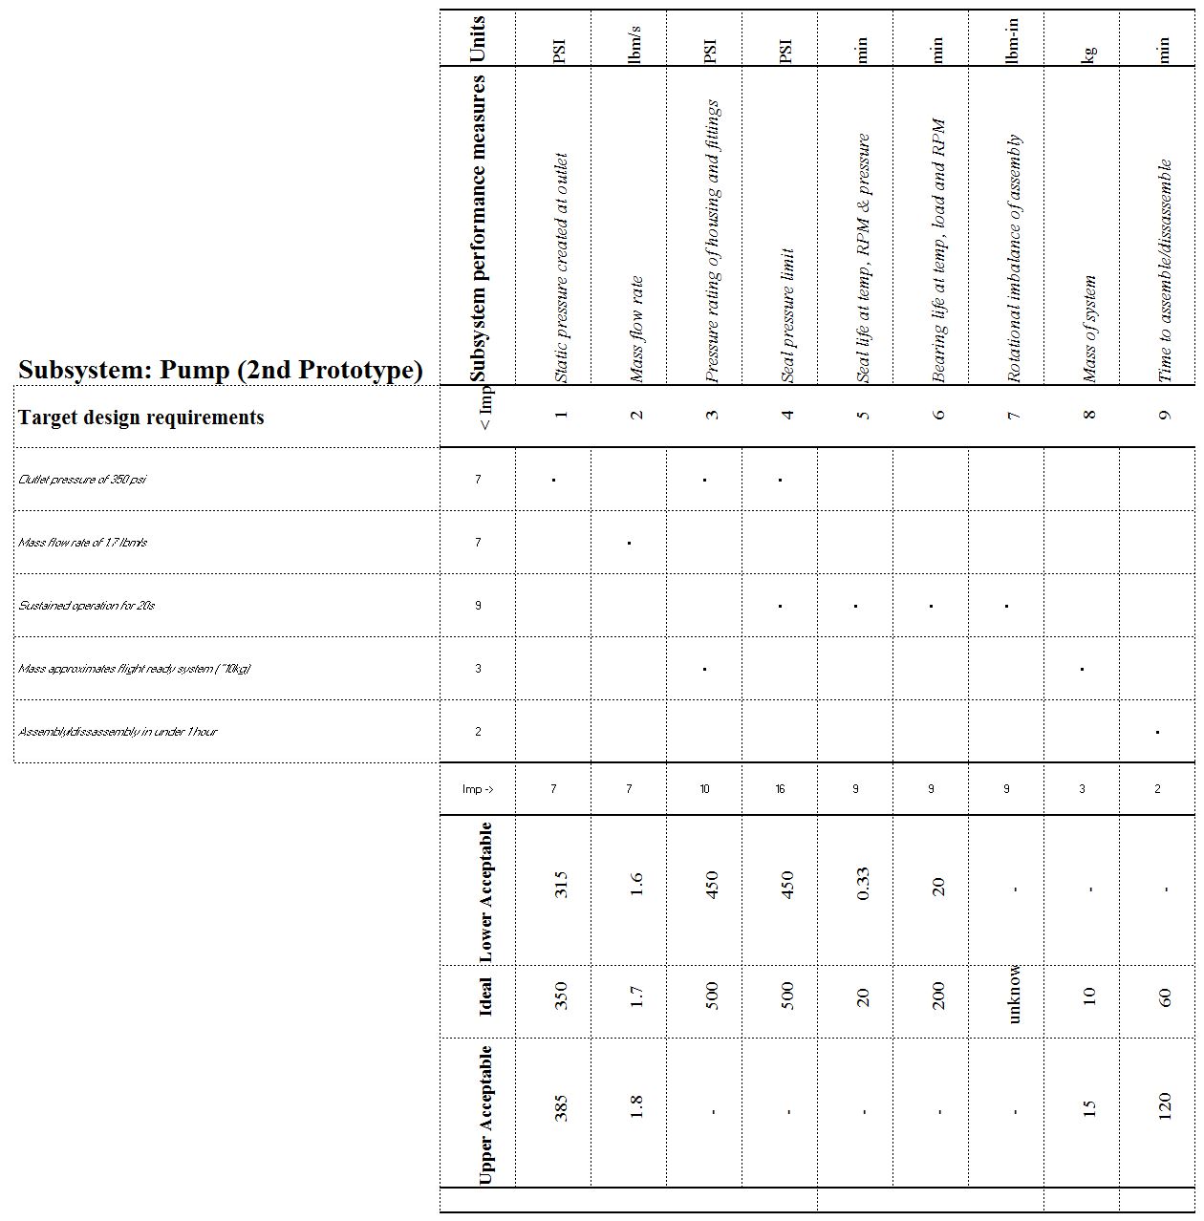
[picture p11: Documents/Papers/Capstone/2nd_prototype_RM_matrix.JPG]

\caption{Requirements/measurements matrix for the second prototype EFS}
\end{center}
\end{figure}

\winsec{Appendix A3:}{ Bill of Materials}
%---------------------------------%
%     New BOM Goes here!     %
%---------------------------------%
\resizebox{\textwidth}{!}{%
\rowcolors{2}{gray!25}{white}
\begin{tabular}{|llcc|}
 \hline
\textbf{Part:}&\textbf{Description:}&\textbf{QTY:}&\textbf{Price:}\\ \hline
\textbf{Motor System:}&&&\\
Motor&Aquastar T20 3T&1&\$97.89\\
Speed controller&AquaStar 240A Water Cooled ESC&1&\$247.07\\
\textbf{Pump: }&&&\\
Aluminum stock&T4048 Aluminum&1&\$31.50\\
\textbf{Control and Data: }&&&\\
Arduino&Arduino Uno&1&\$0.00\\
Solenoid valves&&2&\\
Pressure Transducers (500 psi)&Ashcroft / Grainger G17M0215F2500&2&\$188.75\\
Pressure Gauge (600 psi)&Winters / Amazon PFP663ZRR1&2&\$19.44\\
Pressure Transducer (3000 psi)&Ashcroft / Grainger G17M0215F23000&1&\$188.75\\
Temperature sensors&&5&\\
\textbf{Test Apparatus: }&&&\\
Nitrogen Tank&LuxferL45J&2&\$0.00\\
7/8" to 1/2" compression fitting&Swagelok SS-810-1-10ST&2&\$20.80\\
1/2" to 1/4" tube adapter&Swagelok SS-400-R-8&2&\$11.18\\
1/4" Branch Tee&Swagelok SS-400-3-4TTM&1&\$28.88\\
Needle Valve&Dixon / Amazon MFS102&1&\$60.98\\
Flexible Tubing\&Associated Hose &4R2AT-4-204-B/E&1&\$32.70\\
Pipe Nitrogen&Swagelok SS-T4-S-035-20&12&\$2.57\\
Ferrule Male Connectors&Swagelok SS-400-1-4&5&\$7.35\\
1/4" Ferrule Tee&Swagelok SS-400-3&2&\$23.40\\
1/4" NPT Hex Nipple&Swagelok SS-4-HN&4&\$6.32\\
1/4" NPT/ 1/4" Ferrule Elbow&Swagelok SS-400-2-4&2&\$14.08\\
1/4" Female Tube Adapter&Swagelok SS-4-TA-7-4&4&\$10.15\\
1/2" Female Tube Adapter&Swagelok SS-4-TA-7-8&2&\$13.77\\
1/4" NPT Male Tube Adapter&Swagelok SS-4-TA-1-4&7&\$6.32\\
1/4" Ferrule Cross&Swagelok SS-400-4&1&\$42.54\\
Ethanol Regulator&Swagelok KCY1JRA412A20000&1&\$523.86\\
Oxygen Regulator&Swagelok KCY1JRA412A20000&1&\$523.86\\
Check Valves&Swagelok SS-4C4-1&2&\$48.55\\
Solenoids (Nitrogen)&Asco 8262H080&2&\$98.10\\
Manifold material&Alaskan Copper \& Brass 132132-3P&1&\$62.00\\
Relief Valves&Swagelok SS-4R3A5-SETB&2&\$151.49\\
Vent Valves&Asco 8262H214&2&\$131.08\\
Slic-Tite PTFE Thread Tape&La-Co/Amazon 44094&1&\$2.56\\
1/4" NPT Cross&Parker / Grainger 1/4 KMMOO-SS&1&\$74.55\\
\textbf{Misc: }&&&\\
Wire&Turnigy High Quality 8AWG Silicone Wire&2&\$7.00\\
Bullet connectors&Turnigy 8MM gold connectors&1&\$18.00\\
 \hline
\end{tabular}}

\newpage

\end{document}

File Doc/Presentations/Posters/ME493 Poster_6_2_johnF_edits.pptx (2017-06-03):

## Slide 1

Electric Propellant Feed System (EFS)

Team Members: John C. Froehlich, Jonathan Talik, James Luce, Rawand Rasheed, Mimi Shang and Jordan Roland
Sponsor: Portland State Aerospace Society

Project Objective Statement
The goal of the EFS project is to design, build, and test an electric propellant feed system for the PSAS LV4 liquid fueled bi-propellant rocket engine prototype by June 6, 2017.

Design Features

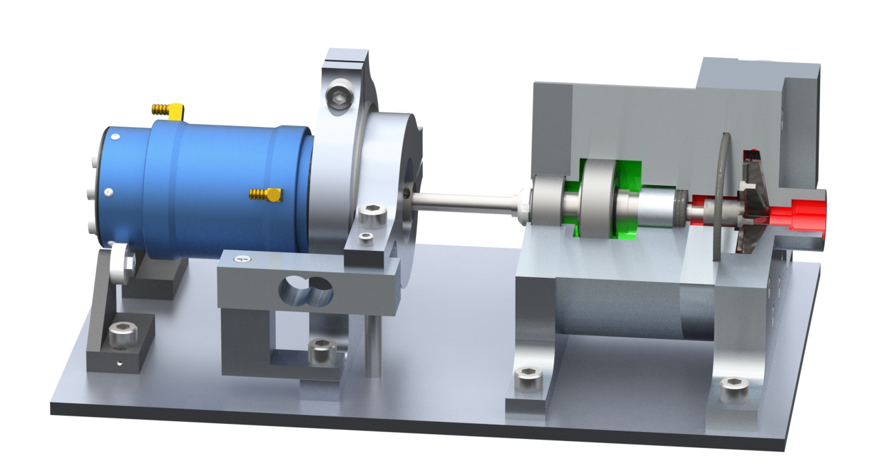
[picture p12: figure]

Water cooled 240 amp brushless DC motor

Floating motor mount

Modular diffuser mount

Barske straight blade impeller

Measured Performance
Show concrete, quantitative evidence that your device works. Show how, and to what degree, your design meets the key customer requirements. Plots, photos of the device in action, or tables of results would be good to add. However, do not cram too much information into the space
This is where you show your convincing evidence for the success of your project

Motivation
Historically, the systems to impel propellants to the combustion chamber of a liquid fueled rocket are based on the employment of turbo-pumps or pressurized gas systems. The complexity and cost of these methods has made building a liquid fuel rocket financially and technically difficult for the amateur rocketry community.
The EFS team is investigating the open source development of a battery powered alternative for use in PSAS’s LV4 bi-propellant rocket (below).

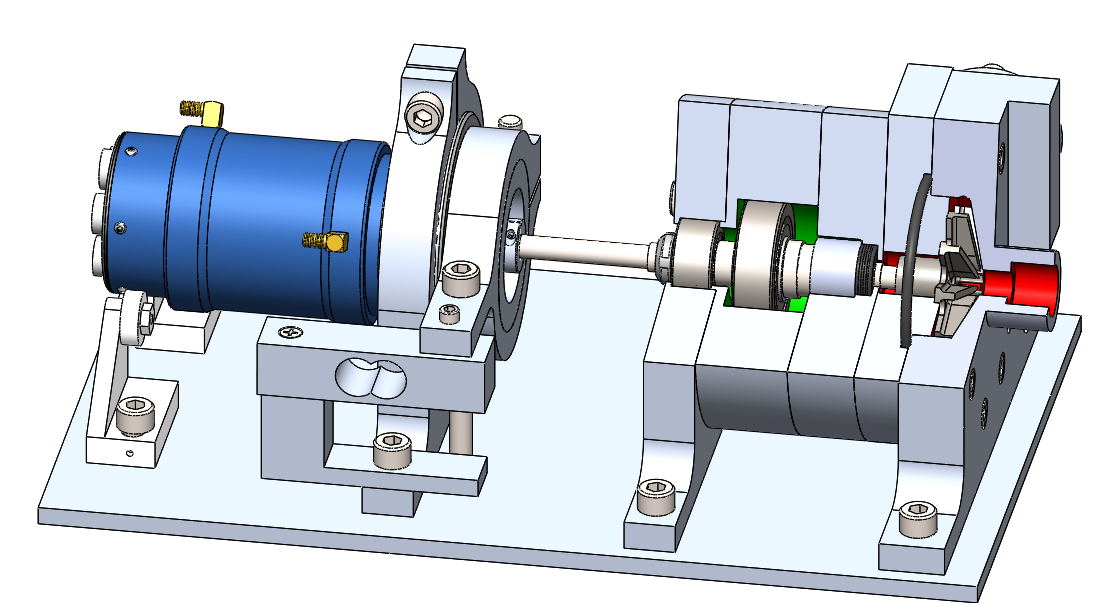
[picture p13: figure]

Key Customer Requirements
- Design, build and test a technology development platform for the electronic propellant feed system.
- Design a pump capable of delivering 350 psi of pressure at 11 GPM to the combustion chamber.
- Pump performance characterization.
- Scalable design for future pump iterations.
- Open source documentation, design artifacts and build information.

Load cell for live shaft torque measurement

Impellers
The EFS system uses an unorthodox Barske straight blade impeller to meet the unusually high head, low flow engine requirements. Final designs were 3D Printed in stainless steel.


Thrust and radial load bearings

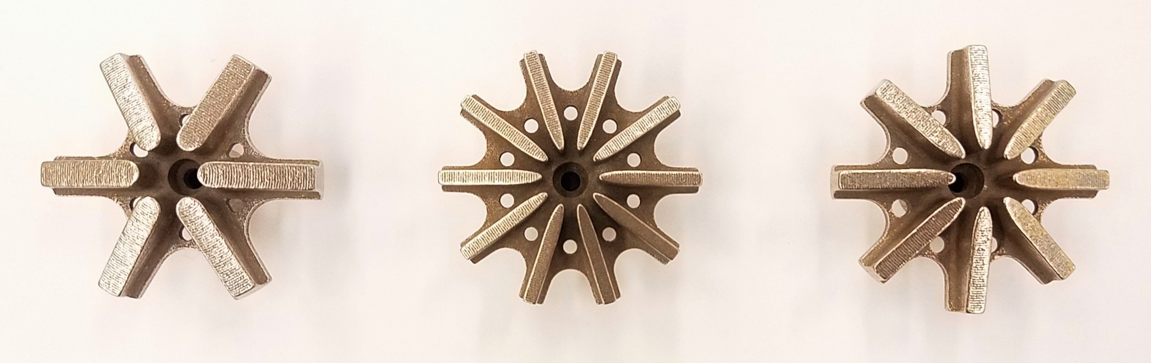
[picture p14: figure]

Experimental Test Platform
- Arduino microcontroller used for motor control and system data acquisition.
- Variables monitored: Suction pressure, discharge pressure, volute and seal cavity pressures, RPM, flow rate, inlet temperature and shaft torque.
- Constant inlet pressure (~45 psi) is provided via a 42 gallon water tank.
- Flow is controlled during testing using a gate valve on the discharge side.
- Motor and speed controller require water cooling .

Shaft seal and Rulon bushing

O-ring seal

Inlet eye

Future Work
- Investigate additional design variations.
- Test pump with PSAS pintle injector.
- Adapt system for cryogenic propellants.
- Scale design to match PSAS LV4 requirements.
- Refine motor control and motor data acquisition.

Acknowledgments

Erin Schmidt Raúl Bayoán Cal Andrew Greenberg | Kris Auclair Mike Chung Haneef Mubarak

Project Website
https://github.com/psas/electric-feed-system

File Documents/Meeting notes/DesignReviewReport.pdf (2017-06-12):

PSAS Electric Feed System Design Review Report

Design Review Meeting Summary
Our team met with our sponsor, PSAS, represented by Erin Schmidt. We discussed where we are in the development of the project: the end of the first prototype design and the beginning of fabrication and assembly. This puts us behind schedule. Consequently, the major outcome of the meeting is that our sponsor recognizes that we may only be able to hit the milestone of conducting one iteration of water testing, though there is still the possibility of conducting a second iteration. We recognized that the first prototype we are creating is well researched and designed and is likely to provide results and documentation that can inform future PSAS efforts on this pump system.

Key Client Requirements
1. A first prototype of an electric motor powered centrifugal water pump system will be created. This pump will be designed to reach the flow rates (~0.04ft^3/s) and pressures (~375 psi) required by the actual LOX and IPA rocket pumps.
i. This requirement will be met if the first prototype is tested and is able to achieve pressure and flow performance similar to design values.
2. The design and testing of the prototype will produce documentation that can inform the design of future water or LOX/IPA prototypes.
i. This requirement will be met by providing well documented procedures and performance results from the first, and if possible, second water prototypes.
3. If possible, the redesign of the water pump for LOX and IPA compatibility should be conducted.
i. This requirement would be met if the team produced a redesign of the pump for LOX and IPA considerations.

Final Deliverables

1. Assembled and tested water pump.
2. Characterized water pump performance to inform next iteration of pump prototype for LOX and IPA pumps.
3. Design of LOX and IPA pumps.

Budget
Total expenditures so far are $1,054.33 out of an anticipated initial budget of $7,900. This $1,054.33 represents much of the anticipated cost of the first prototype. Additional expenses for sensors, fittings, hardware and machining stock are expected before the first water test assembly is completed and tested.

If the project proceeds to the production of a cryogenic LOX pump, there is significant expense expected to procure cryogenic compatible valves, sensors (ex. flow meter), and seals.

For the sake of brevity, a bill of materials is not provided here, but the active BOM can be accessed on the PSAS Github. (https://github.com/psas/electric-feed-system/tree/master/Purchasing)

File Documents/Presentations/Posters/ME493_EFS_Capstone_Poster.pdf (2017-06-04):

Design Features | Measured Performance

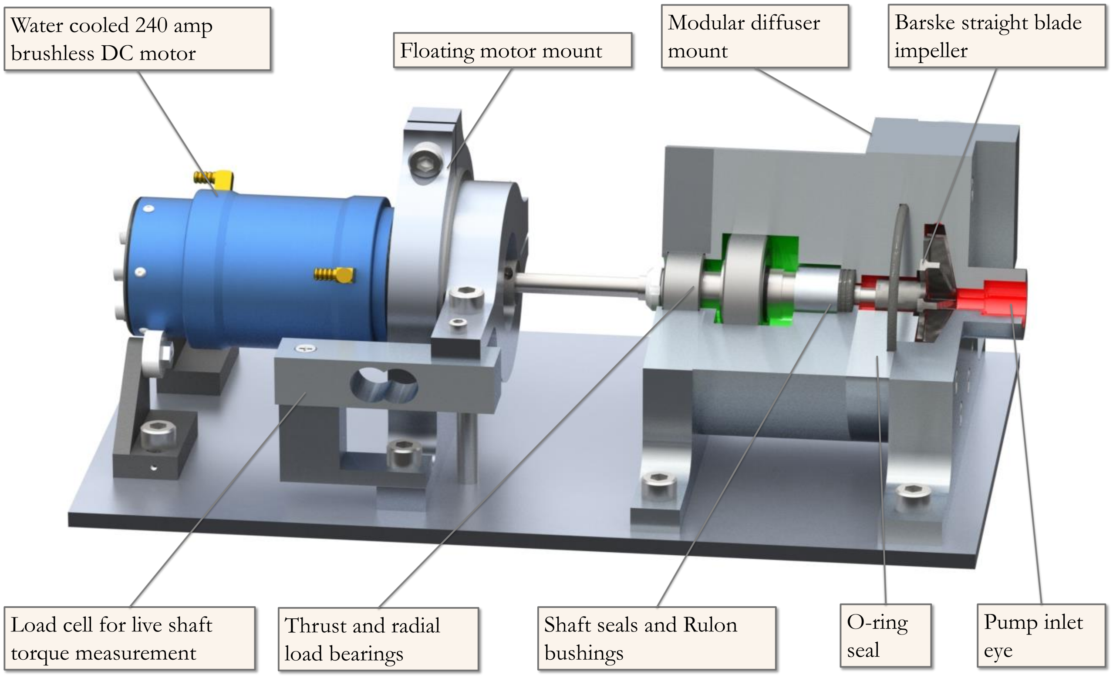
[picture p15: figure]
Water cooled 240 amp brushless DC motor; Load cell for live shaft torque measurement; Floating motor mount; Thrust and radial load bearings; Shaft seals and Rulon bushings; Pump inlet eye; Barske straight blade impeller; O-ring seal; Modular diffuser mount

The electric feed system is actively being tested over a wide range of operating conditions. Initial feedback at lower rotational speeds has provided promising results. A plot of the system running at 17,500 rpm is shown below.

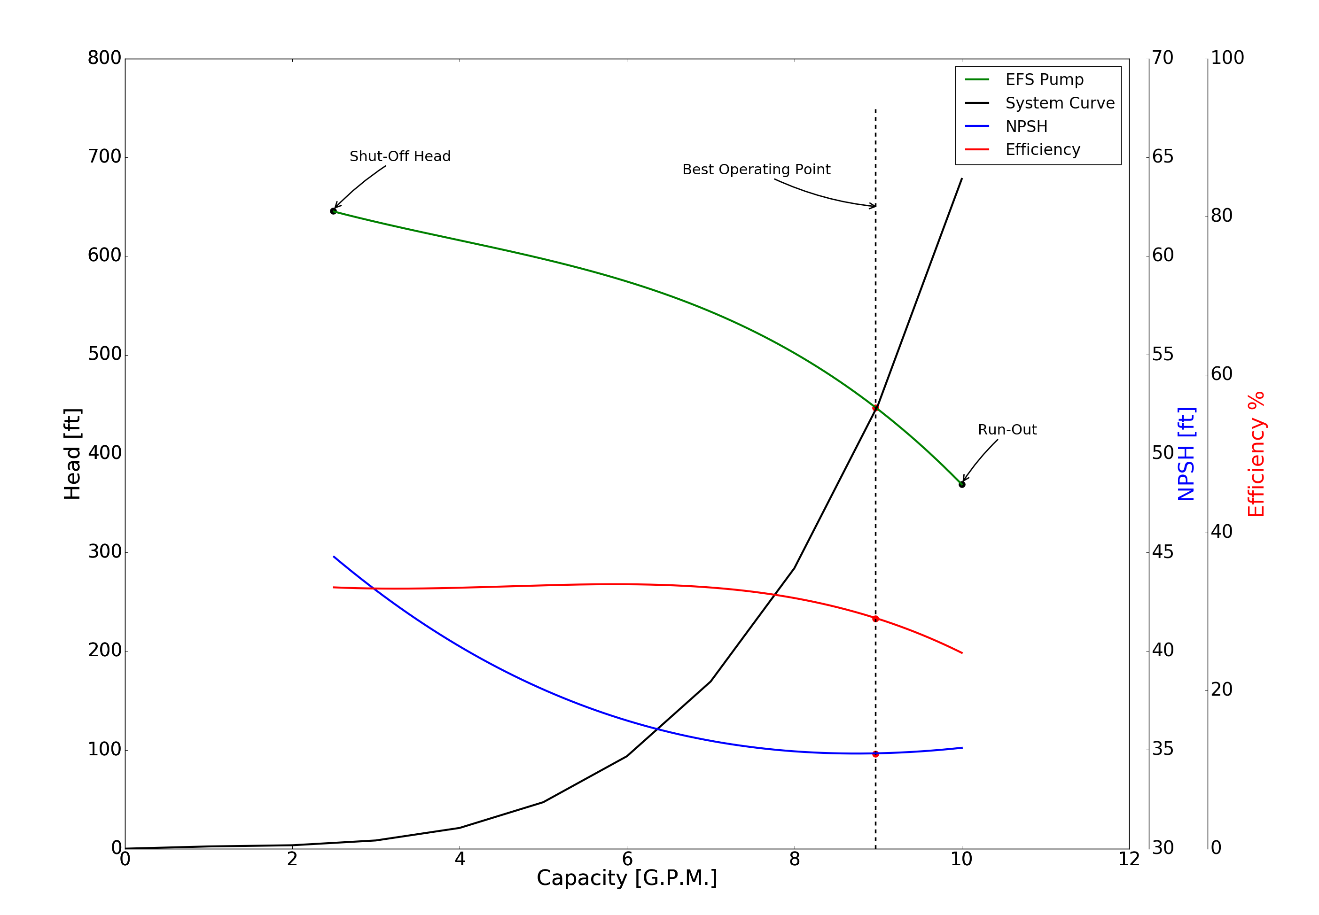
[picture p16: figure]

- The system curve is a function of the static head and the major and minor losses in the system. This curve gives the amount of energy the pump has to create in order to operate at a specified flowrate, Q.
- The pump performance curve describes the relationship between the flowrate and head produced by the actual pump.
- The best operating point is defined as the flow at which the EFS system operates at the highest or optimum efficiency for a given impeller diameter.
- The shut-off (SO) is the head a pump will develop when operating against a closed discharge valve (no flow). Shutt-off kept at 4 GPM to extend life of pump during testing.
- The run-out (RO) is the maximum flow the pump can produce before experiencing severe performance drops.
- The NPSH curve shows the minimum amount of suction pressure to overcome pump entrance losses and cavitation.

## Objective Statement

Electric propellant feed system (EFS) aims to design, build, and test an electric propellant feed system for the PSAS LV3 liquid fueled bi-propellant rocket engine prototype by June 6, 2017.

## Key Customer Requirements

- Design, build and test a technology development platform for the electric propellant feed system.
- Design a pump capable of delivering 350 psi of pressure at ~11 GPM to the LV3 engine.
- Pump performance characterization.
- Attain Scalable design for future pump iterations.
- Harness open source documentation, design artifacts and build information.

## Acknowledgments

Team Members: John C. Froehlich, Jonathan Talik, James Luce, Rawand Rasheed, Mimi Shang and Jordan Roland

# Sponsor: Portland State Aerospace Society

## Project Website

https://github.com/psas/electric-feed-system

# Electric Propellant Feed System

## Motivation

Historically, the systems to impel propellants to the combustion chamber of a liquid fueled rocket are based on the employment of turbo-pumps or pressurized gas systems. The complexity and cost of these methods has made building a liquid fuel rocket financially and technically difficult for the amateur rocket community.

The EFS team is investigating the open source development of a low-cost electric powered alternative for providing the pressure and flow requirements of PSAS’s LV3 rocket.

## Future Work

- Investigate additional design variations.
- Test pump with pintle injector.
- Adapt system for cryogenic propellant conditions.
- Scale for LV4 and future 8kN engine design.
- Refine motor control and motor data acquisition.

We thank our mentors Erin Schmidt, Andrew Greenberg and Raúl Bayoán Cal for their support, Chris Auclair for sharing a wealth of MasterCam knowledge and Mike Chunning for allowing us to live in his machine shop. Funding for this project was provided by Portland State Aerospace Society.

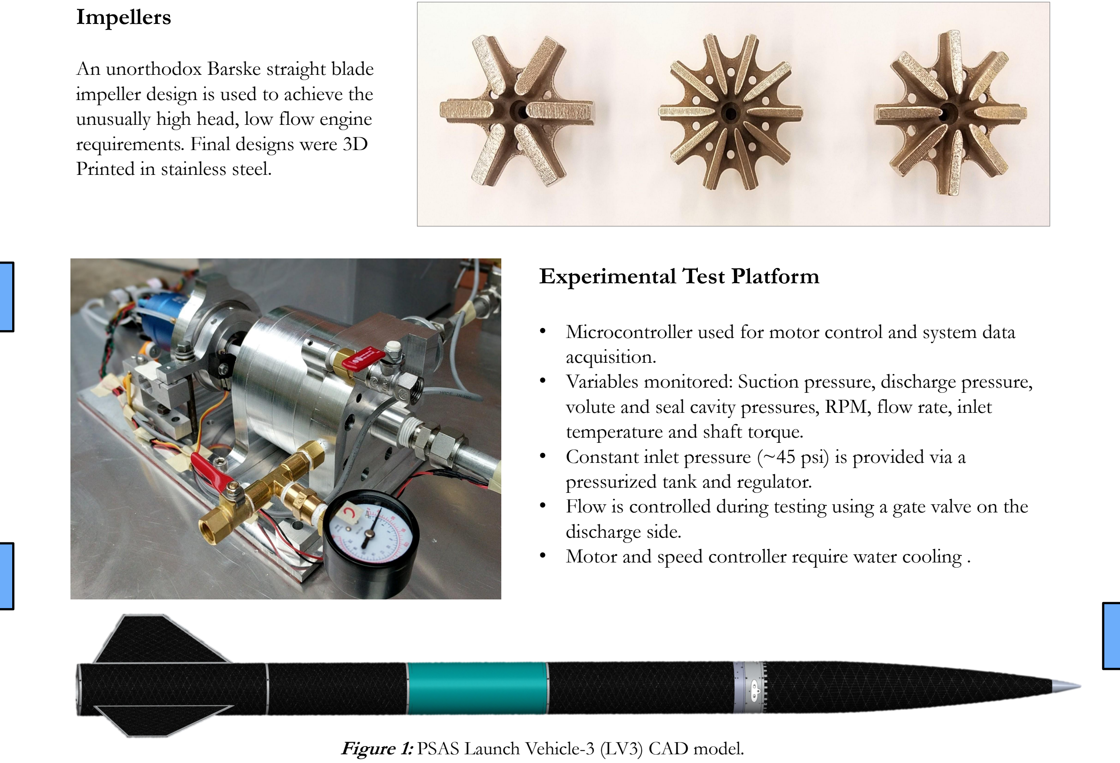
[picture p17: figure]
Impellers; An unorthodox Barske straight blade impeller design is used to achieve the unusually high head, low flow engine requirements. Final designs were 3D Printed in stainless steel.; Experimental Test Platform; acquisition.; temperature and shaft torque.; pressurized tank and regulator.; discharge side.

- Microcontroller used for motor control and system data
- Variables monitored: Suction pressure, discharge pressure, volute and seal cavity pressures, RPM, flow rate, inlet
- Constant inlet pressure (~45 psi) is provided via a
- Flow is controlled during testing using a gate valve on the
- Motor and speed controller require water cooling .

Figure 2: EFS performance characteristics at 17,500 rpm using 11 blade impeller and 8 diffuser.

Figure 1: PSAS Launch Vehicle-3 (LV3) CAD model.

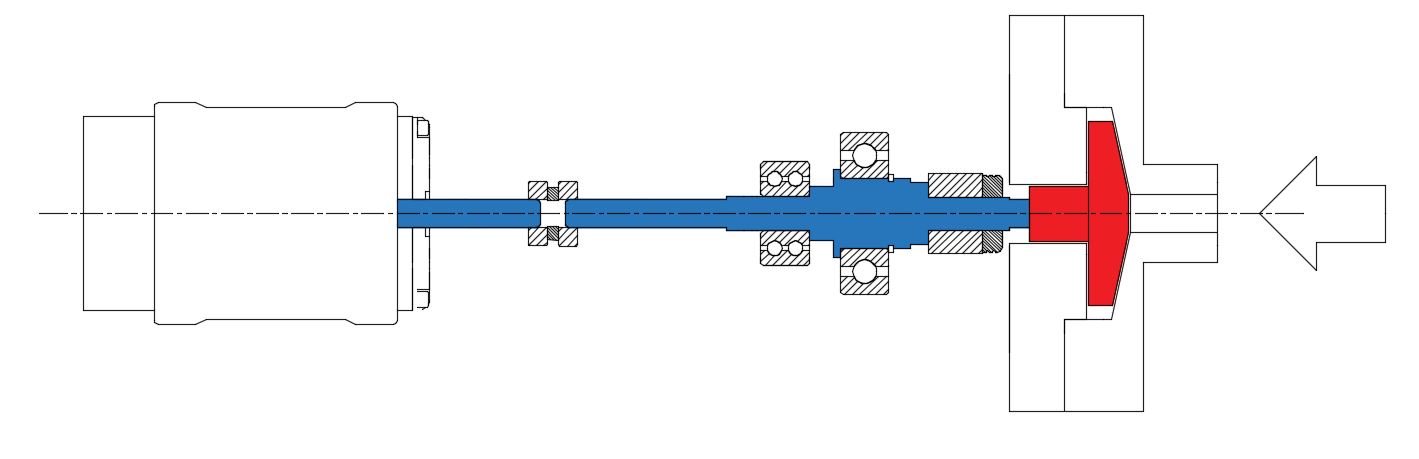
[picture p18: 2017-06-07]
Publicity/Photo/Shaft Schematic bearings.JPG

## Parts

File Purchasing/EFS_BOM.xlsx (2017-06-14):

Part | Price | Quantity Purchased | Total Cost | Manufactuer / Distributor | Part # | Catalog Page # | Links | Notes:
Impellers:
Impeller (1A) | $54.37 | 1 | $54.37 | Shapeways | 1A | N/A |  | Stainless steal
Impeller (2A) | $54.93 | 1 | $54.93 | Shapeways | 2A | N/A |  | Stainless steal
Impeller (3A) | $53.87 | 1 | $53.87 | Shapeways | 3A | N/A |  | Stainless steal
Rotating Assembly:
External Retaining Ring for 20mm Shaft Diameter | $6.72 | 1 | $6.72 | McMaster Carr | 90967A235 | N/A | LINK (https://www.mcmaster.com/) | pkg (5)
Angular-Contact Ball Bearing, Double Row, for 10 mm Shaft Diameter | $29.94 | 1 | $29.94 | McMaster Carr | 8828T111 | N/A
Ball Bearing, for 20 mm Shaft Diameter, 47 mm OD | $6.87 | 2 | $13.74 | McMaster Carr | 5972K105 | N/A
Bearing Locknut, 303 Stainless Steel, M10 x 0.75 mm Thread | $17.12 | 2 | $34.24 | McMaster Carr | 6680K11 | N/A | LINK (https://www.mcmaster.com/)
Tube Fitting, Nut for 1/8" Tube OD | $4.04 | 2 | $8.08 | McMaster Carr | 50715k416 | N/A | LINK (https://www.mcmaster.com/) | Type 316 Stainless Steel 37 Degree
Straight Adapter for 5/8" Tube OD x 1/2 Male Pipe | $8.11 | 2 | $16.22 | McMaster Carr | 50915k332 | N/A |  | Brass Compression Tube Fitting
Oil-Resistant Buna-N O-Ring, 3/32 Fractional Width | $3.68 | 1 | $3.68 | McMaster Carr | 9452k24 | N/A |  | pkg (100)
Dowel Pin, M2 Diameter, 12mm Length | $6.01 | 1 | $6.01 | McMaster Carr | 93600A208 | N/A |  | pkg (25) Metric Type 316 Stainless Steel
Oil-Resistant Buna-N O-Ring, 1/8 Fractional Width, Dash Number 232 | $9.77 | 1 | $9.77 | McMaster Carr | 9452K161 | N/A |  | pkg (50)
Oil-Resistant Shaft Seal, Double-Lip, Steel, 5/8" ID, 1-1/8" OD | $5.70 | 3 | $17.10 | McMaster Carr | 5154T33 | N/A
Oil-Resistant Pump Shaft Seal, | $20.70 | 2 | $41.40 | McMaster Carr | 9281K121 | N/A |  | Keyway for 8mm Diameter Shaft, Black-Oxide Steel
Rigid Shaft Coupling with Keyway | $5.68 | 2 | $11.36 | McMaster Carr | 5395T212 | N/A
37 Degree Flared Tube Fitting, Sleeve for 1/8" Tube OD | $2.60 | 3 | $7.80 | McMaster Carr | 50715K417 | N/A | LINK (https://www.mcmaster.com/) | Type 316 Stainless Steel
Trade No. 6210, for 50 mm Shaft Diameter, 90 mm OD | $23.82 | 1 | $23.82 | McMaster Carr | 5972K129 | NA | LINK (https://www.mcmaster.com/) | Ball Bearing
Mitutoyo 050101, Edge Finder, 3/8" Dia. Shank, .200" Dia. Tip | $12.95 | 2 | $25.90 | Amazon | 50101 | NA | LINK (https://www.amazon.com/gp/product/B002SG7PPC/)
8mm to 8mm elastic shaft coupling | $10.89 | 1 | $10.89 | Amazon | SYNCE007205 | NA | LINK (https://www.amazon.com/gp/product/B06X9WVYLF/)
Flanged sleeve bushing, Rulon, 5/8" ID, | $25.93 | 1 | $25.93 | McMaster Carr | 6362K307 | N/A | LINK (https://www.mcmaster.com/) | Used as the initial spec seal
Electrical:
Motor | $97.89 | 1 | $97.89 | Turnigy/Hobbyking | 9052000029 | N/A | LINK (https://hobbyking.com/en_us/turnigy-aquastar-t20-3t-730kv-1280kv-water-cooled-brushless-motor.html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)
Electronic speed controller | $247.07 | 1 | $247.07 | Turnigy/Hobbyking | 9163000003-0 | N/A | LINK (https://hobbyking.com/en_us/turnigy-aquastar-240a-water-cooled-esc.html)
Wire (8GA) | $3.50 | 2 | $7.00 | Turnigy/Hobbyking | 171000710-0 | N/A | LINK (https://hobbyking.com/en_us/turnigy-high-quality-8awg-silicone-wire-1m-black.html)
Bullet Connectors | $18.00 | 1 | $18.00 | Turnigy/Hobbyking | AM8mm | N/A | LINK (https://hobbyking.com/en_us/8mm-gold-connectors-12-pack.html)
Batteries | $157.57 | 2 | $315.14 | Turnigy/Hobbyking | 9067000112-0 | N/A | LINK (https://hobbyking.com/en_us/turnigy-graphene-12000mah-6s-15c-w-5-5mm-bullet-connector.html)
Ashcroft G2500PSI Pressure Transmitter, 0 to 500 psi, 4-20mA | $153.85 | 1 | $153.85 | Cole-Palmer | UX-68900-56 | N/A | LINK (https://www.coleparmer.com/i/ashcroft-g2500psi-pressure-transmitter-0-to-500-psi-4-20ma/6890056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)
Thermocouple Type-K | $17.99 | 1 | $17.99 | Amazon | B01DCJE7E0 | N/A | LINK (https://www.amazon.com/gp/product/B01DCJE7E0/ref=oh_aui_detailpage_o01_s00?ie=UTF8&psc=1)
Arduino Mega | $11.99 | 1 | $11.99 | Amazon | ATMEGA16U2 | N/A | LINK (https://www.amazon.com/gp/product/B01H4ZLZLQ/ref=oh_aui_detailpage_o02_s00?ie=UTF8&psc=1)
Thermocouple Amplifier breakout board | $14.95 | 1 | $14.95 | Adafruit | MAX6675 | N/A | LINK (https://www.adafruit.com/product/269)
1k potentiometer | $1.40 | 2 | $2.80 | URS Electronics Inc | pc72b | N/A
10 digital pot | $1.50 | 2 | $3.00 | URS Electronics Inc | com-10613 | N/A
9 pos .100 kk conn housing w lock ramp | $0.19 | 10 | $1.90 | URS Electronics Inc | 22-01-3097 | N/A
22-30 awg female kk crimp terminal | $0.10 | 100 | $10.00 | URS Electronics Inc | 08-50-0114 | N/A
paste flux | $3.00 | 1 | $3.00 | URS Electronics Inc | 26-331770 | N/A
connector jumper wire kit, 6" m/f | $1.95 | 1 | $1.95 | URS Electronics Inc | prt-12794 | N/A
connector jumper wire kit, 6" f/f | $1.95 | 1 | $1.95 | URS Electronics Inc | prt-12796 | N/A
connector jumper wire kit, 6" m/m | $1.95 | 1 | $1.95 | URS Electronics Inc | prt-12795 | N/A
tactile button assortment, ten buttons | $1.00 | 1 | $1.00 | URS Electronics Inc | com-10302 | N/A
medium GTE (goes to eleven) knob | $1.25 | 2 | $2.50 | URS Electronics Inc | com-11949 | N/A
Load Cell Amplifier | $13.95 | 1 | $13.95 | Amazon | HX711 | N/A | LINK (https://www.amazon.com/gp/product/B01K7Z02IW/ref=oh_aui_detailpage_o04_s00?ie=UTF8&psc=1)
Mechanical:
Bearing plate | $0.00 | 1 | $0.00 | In house | 1BPA | N/A
Impeller lower housing | $0.00 | 1 | $0.00 | In house | 1LHA | N/A
Impeller upper housing | $0.00 | 1 | $0.00 | In house | 1UHA | N/A
Motor mount | $0.00 | 1 | $0.00 | In house | 1MMA | N/A
Seal plates | $0.00 | 1 | $0.00 | In house | 1SPA | N/A
Impeller Shaft | $0.00 | 1 | $0.00 | In house | 1SFTA | N/A
Raw Materials:
AL FLAT 6061T6 1.00 X 6.00 | $3.45 | 2 | $6.90 | Metal Supermarket | AF6061/16 | N/A |  | LGTH UNIT INCH
AL FLAT 6061T6 1.00 X 6.00 | $3.45 | 2 | $6.90 | Metal Supermarket | AF6061/16 | N/A |  | LGTH UNIT INCH
AL FLAT 6061T6 1.00 X 6.00 | $3.45 | 2 | $6.90 | Metal Supermarket | AF6061/16 | N/A |  | LGTH UNIT INCH
AL FLAT 6061T6 1.00 X 6.00 | $3.45 | 1 | $3.45 | Metal Supermarket | AF6061/16 | N/A |  | LGTH UNIT INCH
AL FLAT 6061T6 2.00 X 5.00 | $5.30 | 1 | $5.30 | Metal Supermarket | AF6061/25 | N/A |  | LGTH UNIT INCH
AL ROUND 6061T6 2.500 | $2.67 | 1 | $2.67 | Metal Supermarket | AF6061/212 | N/A |  | LGTH UNIT INCH
AL ROUND 6061T6 2.00 | $1.65 | 1 | $1.65 | Metal Supermarket | AF6061/2 | N/A |  | LGTH UNIT INCH
AL ROUND 6061T6 1.00 | $2.18 | 1 | $2.18 | Metal Supermarket | SR316/1 | N/A |  | LGTH UNIT INCH
SS ROUND 303 1x6.25 | $10.14 | 1 | $10.14 | Metal Supermarket | SR303/1 | N/A
SS ROUND 303 1x6.25 | $10.00 | 1 | $10.00 | Metal Supermarket | SR303/1 | N/A
Plumbing:
1/8" Tube OD x 1/8 NPT Male | $13.54 | 1 | $13.54 | Swagelok\Mcmaster Carr | 50715K411 | N/A | LINK (https://www.mcmaster.com/)
On/Off Ball Valve | $10.57 | 1 | $10.57 | McMaster Carr | 4067T31 | N/A | LINK (https://www.mcmaster.com/)
Branch Tee, 5/8 in. Tube OD x 1/2 in. Female NPT | $73.18 | 1 | $73.18 | Swagelok | SS-1010-3TTF | N/A | LINK (https://www.swagelok.com/en/catalog/Product/Detail?part=SS-1010-3TTF) | Stainless Steel Swagelok Tube Fitting, Female Branch Tee, 5/8 in. Tube OD x 5/8 in. Tube OD x 1/2 in. Female NPT
Right-Angle Tee Adapter, 1/2 NPT Female x Male | $17.40 | 1 | $17.40 | McMaster Carr | 50785K228 | N/A | LINK (https://www.mcmaster.com/) | High-Pressure Brass Pipe Fitting, Sealant, Right-Angle Tee Adapter, 1/2 NPT Female x Male
Hex Bushing Adapter, 1/2 NPT Male x 1/4 NPT Female | $2.54 | 2 | $5.08 | McMaster Carr | 50785K65 | N/A | LINK (https://www.mcmaster.com/)
Male Connect, 5/8 in. Tube OD x 1/2 in. Male NPT | $18.95 | 1 | $18.95 | Swagelok | SS-1010-1-8 | N/A | LINK (https://www.swagelok.com/en/catalog/Product/Detail?part=SS-1010-1-8) | Stainless Steel Swagelok Tube Fitting, Male Connector, 5/8 in. Tube OD x 1/2 in. Male NPT
Branch Tee, 5/8 in. Tube OD x 1/2 in. Female NPT | $73.18 | 1 | $73.18 | Swagelok | SS-1010-3TTF | N/A | LINK (https://www.swagelok.com/en/catalog/Product/Detail?part=SS-1010-3TTF)
Hollow Plug with External Hex Drive, 1/2 NPT | $2.81 | 1 | $2.81 | McMaster Carr | 50785K24 | N/A | LINK (https://www.mcmaster.com/)
Solid Plug with External Hex Drive, 1/2 NPT | $3.69 | 1 | $3.69 | McMaster Carr | 50785K337 | N/A | LINK (https://www.mcmaster.com/)
Male Connector, 1/2 in. Tube OD x 3/8 in. Male NPT | $15.32 | 1 | $15.32 | Swagelok | SS-810-1-6 | N/A | LINK (https://www.swagelok.com/en/catalog/Product/Detail?part=SS-810-1-6) | Stainless Steel Swagelok Tube Fitting, Male Connector, 1/2 in. Tube OD x 3/8 in. Male NPT
Branch Tee, 1/2 in. Tube OD x 1/2 in. Female NPT | $56.31 | 1 | $56.31 | Swagelok | SS-810-3-8TTF | N/A | LINK (https://www.swagelok.com/en/catalog/Product/Detail?part=SS-810-3-8TTF) | Stainless Steel Swagelok Tube Fitting, Female Branch Tee, 1/2 in. Tube OD x 1/2 in. Tube OD x 1/2 in. Female NPT
Right-Angle Tee Adapter, 1/2 NPT Female x Male | $17.40 | 1 | $17.40 | McMaster Carr | 50785K228 | N/A | LINK (https://www.mcmaster.com/)
Gate Valve Pressure Class 300, Rising Stem, 1/2 NPT Female | $66.39 | 1 | $66.39 | McMaster Carr | 4606K13 | N/A | LINK (https://www.mcmaster.com/)
Tube Fitting, Male Connector, 1/2 in. Tube OD x 1/2 in. Male NPT | $16.98 | 2 | $33.96 | Swagelok | SS-810-1-8 | N/A | LINK (https://www.swagelok.com/en/catalog/Product/Detail?part=SS-810-1-8)
Aluminum Tubing 5/8" OD, 0.065" Wall Thickness (6ft) | $24.85 | 1 | $24.85 | McMaster Carr | 89965K571 | N/A | LINK (https://www.mcmaster.com/)
Aluminum Tubing 1/2" OD, 0.049" Wall Thickness (6ft) | $16.20 | 1 | $16.20 | McMaster Carr | 89965K25 | N/A | LINK (https://www.mcmaster.com/)
Stainless Steel Case, Liquid, 2-1/2" Dial | $49.39 | 1 | $49.39 | McMaster Carr | 3795K13 | N/A | LINK (https://www.mcmaster.com/)
Flotec FP7110T 19-Gallon Pre-Charged Water Tank | $131.82 | 1 | $131.82 | Amazon | NA | N/A | LINK (https://www.amazon.com/Flotec-FP7110T-19-Gallon-Pre-Charged-Water/dp/B0002YXAQA?rps=1)
300 psi 1/4 npt dry gauge | $4.99 | 2 | $9.98 | Harbor Freight | 68250 | N/A
1/4 full port ball valve | $3.99 | 2 | $7.98 | Harbor Freight | 68254 | N/A
1/4 female pipe t connection | $1.99 | 2 | $3.98 | Harbor Freight | 68197 | N/A
tire chuck with lock on | $2.99 | 1 | $2.99 | Harbor Freight | 62626 | N/A
1/4 x 1/4 female pipe coupling | $1.99 | 2 | $3.98 | Harbor Freight | 68200 | N/A
1/4x1/4 male pipe coupling | $0.99 | 2 | $1.98 | Harbor Freight | 68198 | N/A
vinyl tubing 5/16I x 20' | $4.93 | 1 | $4.93 | Home Depot | 841804100264 | N/A
PVC riser 3/4 x 18 | $1.57 | 1 | $1.57 | Home Depot | 46878381650 | N/A
PVC riser 1/2 x 4 | $0.58 | 1 | $0.58 | Home Depot | 46878380844 | N/A
Nipple 3/4 x 4 riser | $0.65 | 2 | $1.30 | Home Depot | 46878380998 | N/A
1/2 full port valve 600 psi | $8.86 | 1 | $8.86 | Home Depot | 820633959694 | N/A
3/4 full port valve 600 psi | $13.57 | 1 | $13.57 | Home Depot | 820633959687 | N/A
3/4x1/2x3/4 tee | $4.09 | 1 | $4.09 | Home Depot | 32888308947 | N/A
PTFE 66 ft tape | $0.99 | 2 | $1.98 | O'Riellys | PFM 20100 | N/A
1.0 - 16 gpm Flow Range, 1/2" NPT Female Flowmeter | $105.00 | 1 | $105.00 | Amazon | H624-016 | N/A | LINK (https://www.amazon.com/gp/product/B005K2MRGS/ref=oh_aui_detailpage_o05_s00?ie=UTF8&psc=1)
Fasteners:
 |  |  |  |  |  | N/A
 |  |  |  |  |  | N/A
Tooling:
Micro boring bar | $28.80 | 1 | $28.80 | Amazon | QBB-1801500 | N/A | LINK (https://www.amazon.com/Micro-100-BB-1801500-Diameter-Projection/dp/B00Q8KO22S)
3/8 x .200 edge finder | $17.00 | 1 | $17.00 | Hall Tool | Gen 263 | NA
1/8" Mill Diameter, 3/8" Shank Diameter, 2-5/16" Overall Length | $20.25 | 1 | $20.25 | McMaster Carr | 8838A11 | NA | LINK (https://www.mcmaster.com/) | TiAlN Coated High-Speed Steel Two-Flute End Mill
1/4" Diameter x 1" Long Shoulder, 10-32 Thread Size | $2.63 | 3 | $7.89 | McMaster Carr | 91259A174 | NA | LINK (https://www.mcmaster.com/) | Alloy Steel Shoulder Screw
Misc:
Thread seal tape | $0.99 | 1 | $0.99 | Ace | 4237624 | N/A | N/A
Digital Photo Frame | $49.99 | 1 | $49.99 | Amazon | 91259A174 | N/A | LINK
TOTAL: |  |  |  | $2367.47

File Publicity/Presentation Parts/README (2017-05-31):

This folder contains parts used for the presentation table at the capstone symposium.

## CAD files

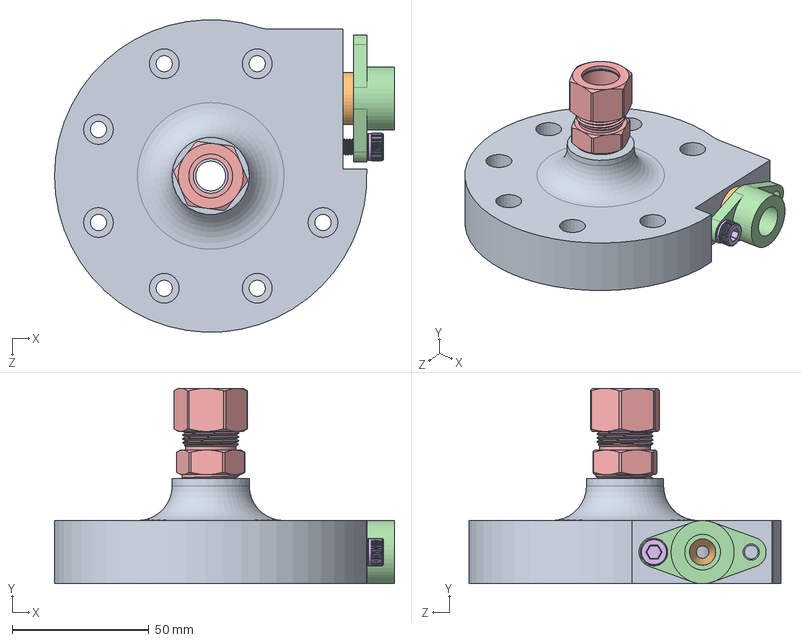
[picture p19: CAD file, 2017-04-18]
2.2 kN/CAD/v5/impeller housing/housing assembly for fab check.SLDASM
124.4 x 71.5 x 114.2 mm
housing_v5_interchangeable_diffuser - for CNC
12_degree_diffuser
9452K240_OIL-RESISTANT BUNA-N MULTIPURPOSE O-RING
diffuser flange
tank to inlet 50915K332_BRASS COMPRESSION TUBE FITTING
m6x20mm

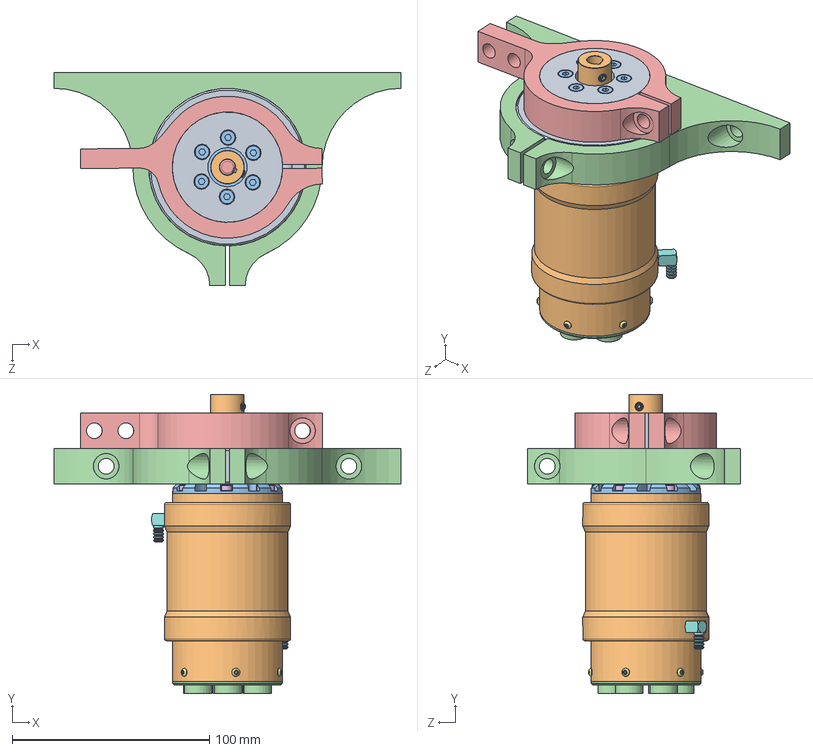
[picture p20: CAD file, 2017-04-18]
2.2 kN/CAD/v5/motor mount/motor mount for torque assembly.SLDASM
176.0 x 151.9 x 108.0 mm
motor mount_v5_for_torque
Casing
Cap
Electical
Shaft
91251A243_BLACK-OXIDE ALLOY STEEL SOCKET HEAD CAP SCREW x 6
91255A075_ALLOY STEEL BUTTON-HEAD SOCKET CAP SCREW x 6
Water_Jacket x 2
5972K114_BALL BEARING
5395T212_SET SCREW RIGID SHAFT COUPLING
M4x8 x 6
motor mount_v5_for_torque_part_2
motor mount_v5_for_torque_part_3

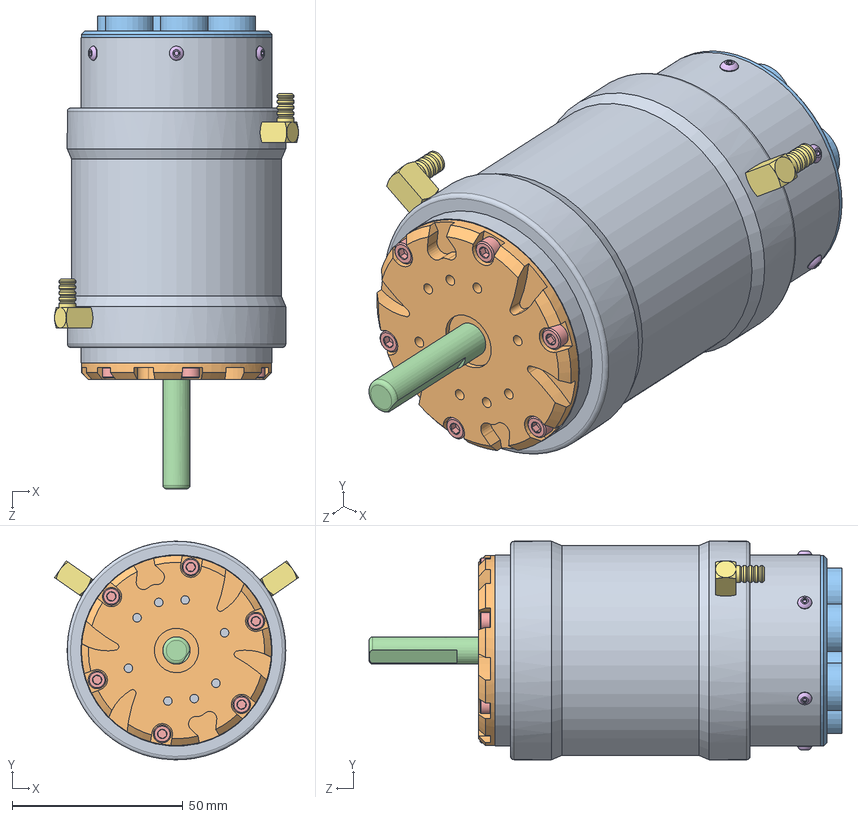
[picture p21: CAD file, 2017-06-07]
2.2 kN/CAD/v5/motor/Aquastarr_T20.SLDASM
71.4 x 64.0 x 138.4 mm
Casing
Cap
Electical
Shaft
91251A243_BLACK-OXIDE ALLOY STEEL SOCKET HEAD CAP SCREW x 6
91255A075_ALLOY STEEL BUTTON-HEAD SOCKET CAP SCREW x 6
Water_Jacket x 2

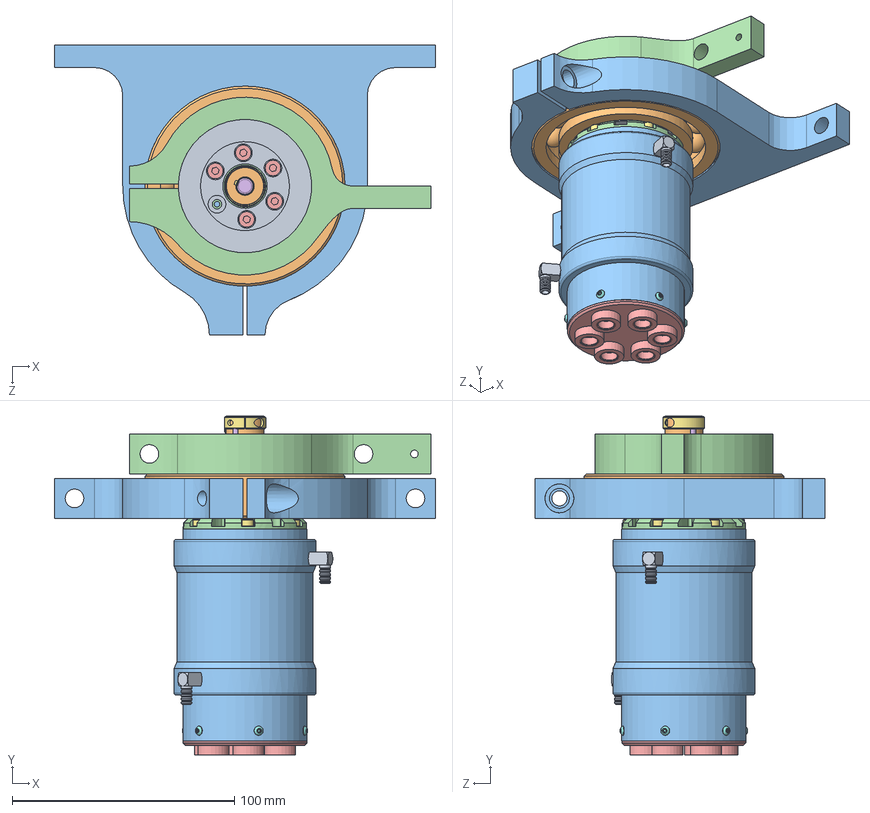
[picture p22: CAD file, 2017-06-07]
2.2 kN/CAD/v6 manufacturing/assemblies/Assemblies/motor mount assembly v6.SLDASM
171.4 x 152.4 x 130.5 mm
motor mount_v6_adapter
50mm 5972K129_BALL BEARING
Casing
Cap
Electical
Shaft
91251A243_BLACK-OXIDE ALLOY STEEL SOCKET HEAD CAP SCREW x 6
91255A075_ALLOY STEEL BUTTON-HEAD SOCKET CAP SCREW x 6
Water_Jacket x 2
motor mount_v6
motor mount_v6_torque arm
M4x8 x 5
60635K860_HIGH-MISALIGNMENT FLEXIBLE SHAFT COUPLING
60635K103_HIGH-MISALIGNMENT FLEXIBLE SHAFT COUPLING x 2

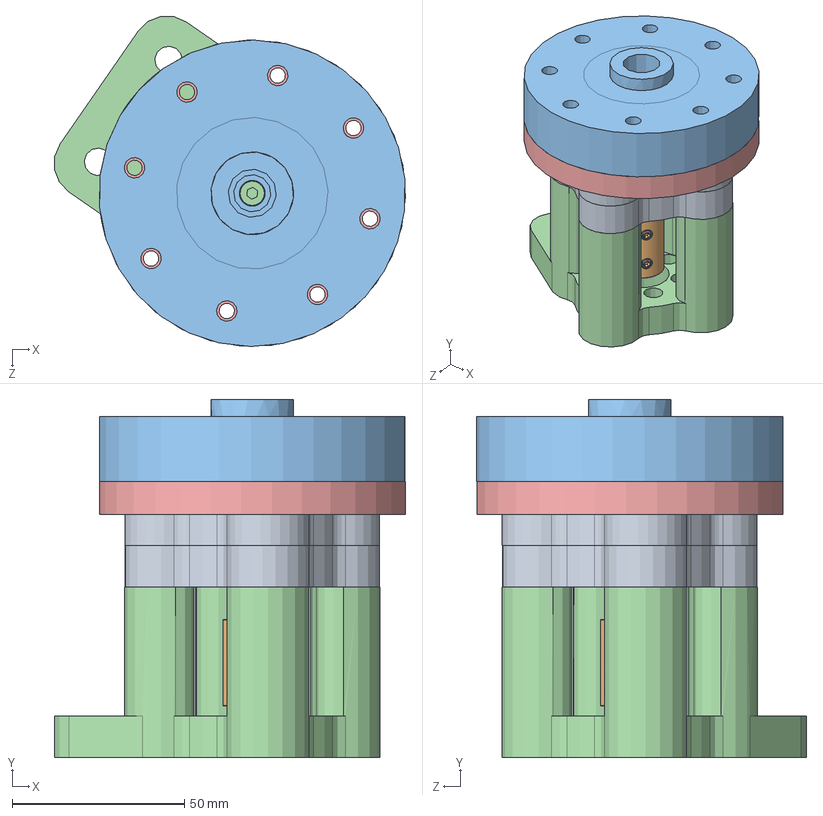
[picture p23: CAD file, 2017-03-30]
CAD/water_test_assembly_JL_3_14_17.SLDASM
101.8 x 103.8 x 95.7 mm
bearing_plate_JL_3_14_17
impeller_shaft_JL_3_13_17
impeller_parameterized_JL_3_13_17
M4x8
big_seal_JL_3_14_17
seal_JL_3_5_17
impeller_dowel
bearing_JL_3_5_17
small_seal_plate_JL_3_14_17
5395T212_SET SCREW RIGID SHAFT COUPLING
impeller_housing_v3_JL_3_28_17
motor mount_JL__v2_3_29_17
big_seal_plate_JL_3_14_17

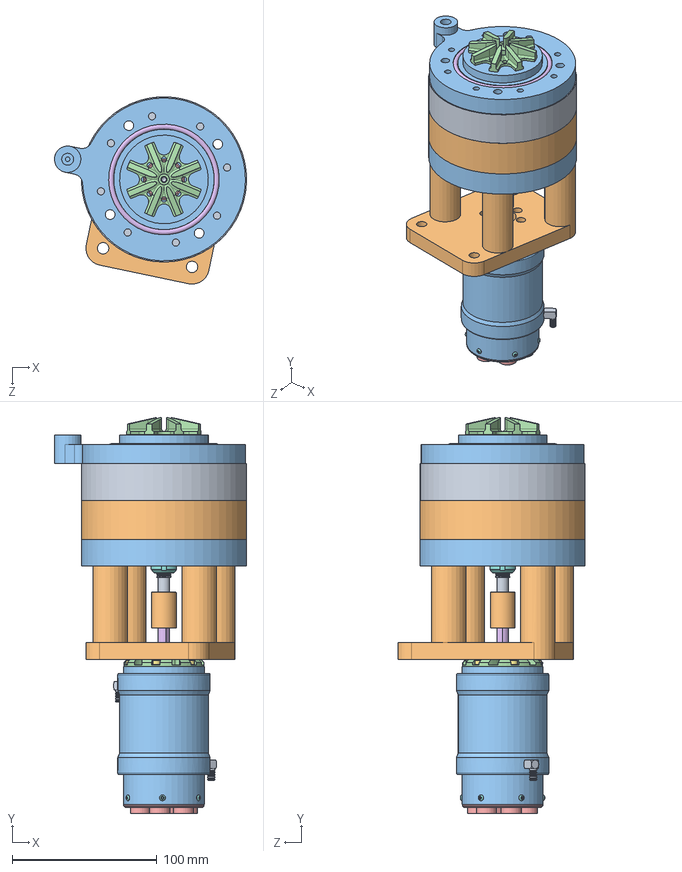
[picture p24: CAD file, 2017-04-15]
2.2 kN/CAD/v5/Assembly final john.SLDASM
132.9 x 273.9 x 129.5 mm
shaft_final
20mm Nonlocating Bearing Plate
Locating Bearing Plate
5972K105_20mm_nonlocating bearing
8828T111_Locating Bearing
90967A235_20mm snap ring
6343K940_10mm collar
lower seal plate john
motor mount_JL__v3
Casing
Cap
Electical
Shaft
91251A243_BLACK-OXIDE ALLOY STEEL SOCKET HEAD CAP SCREW x 6
91255A075_ALLOY STEEL BUTTON-HEAD SOCKET CAP SCREW x 6
Water_Jacket x 2
5395T212_SET SCREW RIGID SHAFT COUPLING
upper_seal_plate_v5
impeller_v5_based_on_2A
upper_seal_v5
9452K161_OIL-RESISTANT BUNA-N MULTIPURPOSE O-RING

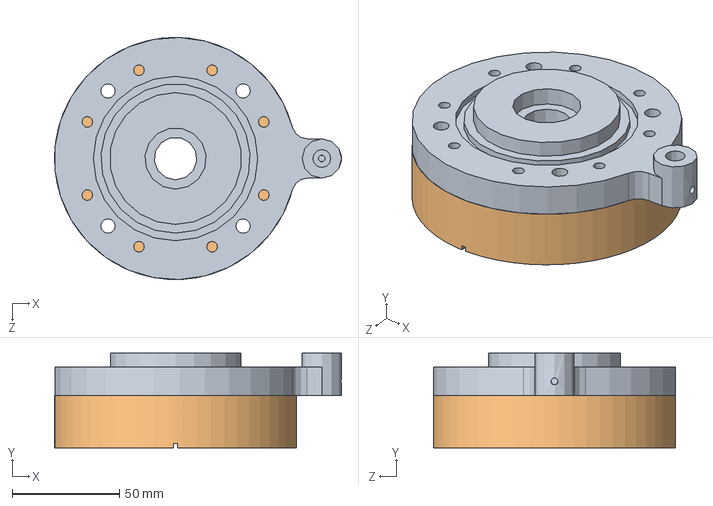
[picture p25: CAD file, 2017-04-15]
2.2 kN/CAD/v5/seal plates/seal assembly.SLDASM
133.6 x 44.2 x 112.7 mm
upper_seal_plate_v5
lower_seal_plate_v5

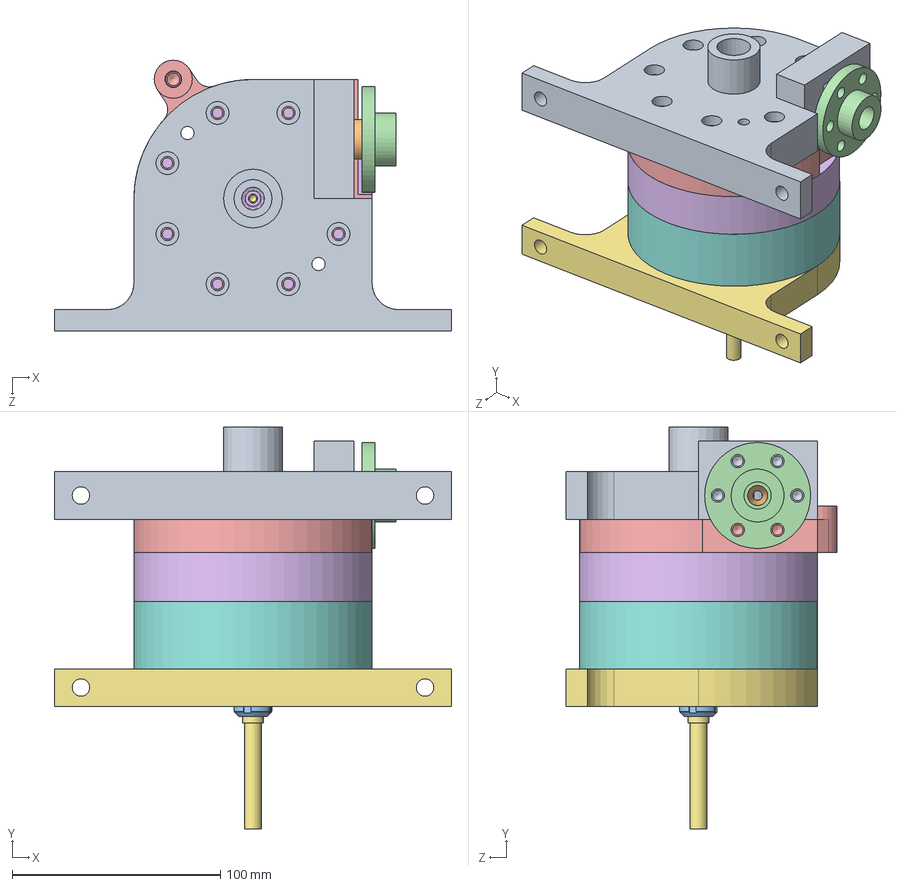
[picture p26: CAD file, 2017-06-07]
2.2 kN/CAD/v6 manufacturing/assemblies/Assemblies/upper assembly - james.SLDASM
190.5 x 192.7 x 129.9 mm
housing_v6_CNC_with mount flanges - new outlet mount
12_degree_diffuser
9452K240_OIL-RESISTANT BUNA-N MULTIPURPOSE O-RING
diffuser flange_v6_new
upper seal plate v6
lower seal plate v6
Locating Bearing Plate v6
20mm Nonlocating Bearing Plate
5972K105_20mm_nonlocating bearing
8828T111_Locating Bearing
6343K940_10mm collar
90967A235_20mm snap ring
lower_seal_mcmaster_john_crane_clone
impeller_v5_for_fab_3A_10_vane
shaft_pump_v6
oring
6362K307_rulon_upper_seal_

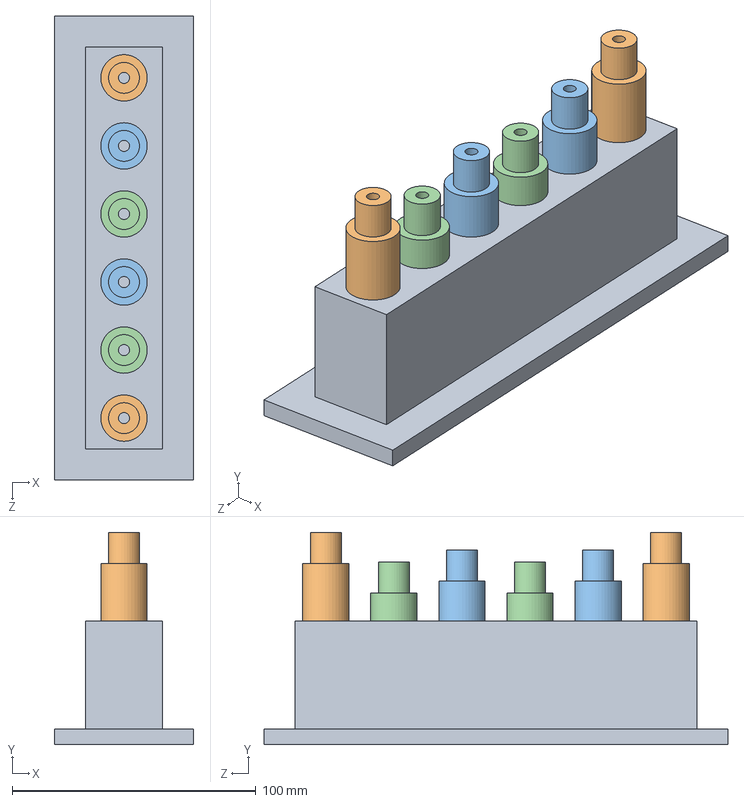
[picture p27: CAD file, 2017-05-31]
Publicity/Presentation Parts/Diffuser_Holder_With_Diffusers.SLDASM
57.2 x 87.1 x 190.5 mm
Diffuser_Holder
8_degree_diffuser x 2
10_degree_diffuser x 2
12_degree_diffuser x 2

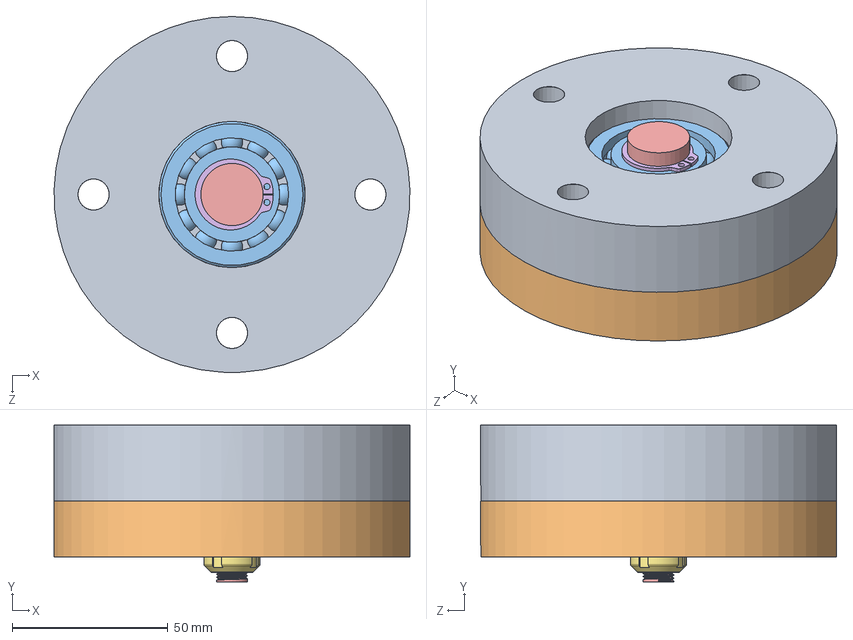
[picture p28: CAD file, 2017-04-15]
2.2 kN/CAD/v5/Bearing System/bearing system.SLDASM
114.2 x 50.3 x 114.3 mm
20mm Nonlocating Bearing Plate
Locating Bearing Plate
5972K105_20mm_nonlocating bearing
8828T111_Locating Bearing
Shaft_Bearing System
90967A235_20mm snap ring
6343K940_10mm collar

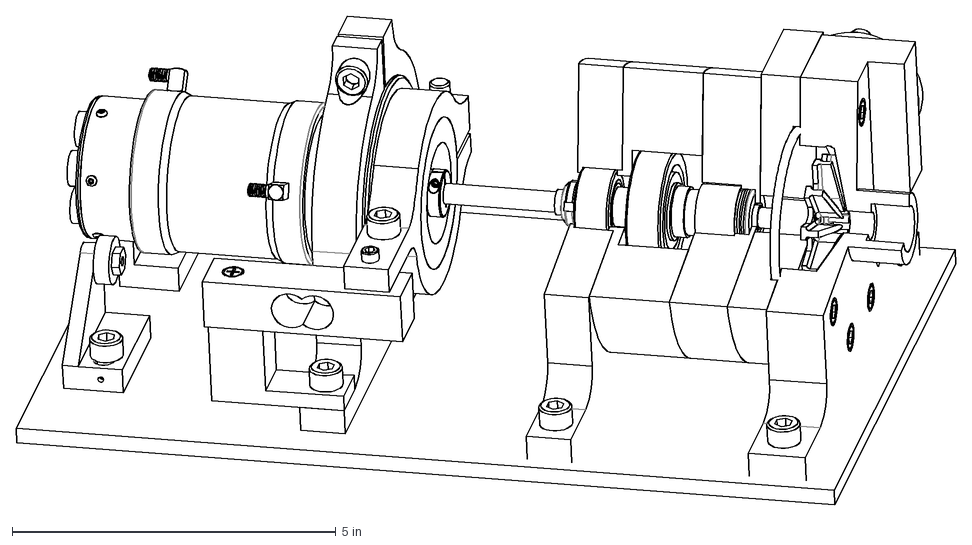
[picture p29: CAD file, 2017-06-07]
2.2 kN/CAD/v6 manufacturing/assemblies/Diagrams/Section Assembly.DXF
14.5 x 7.54 in

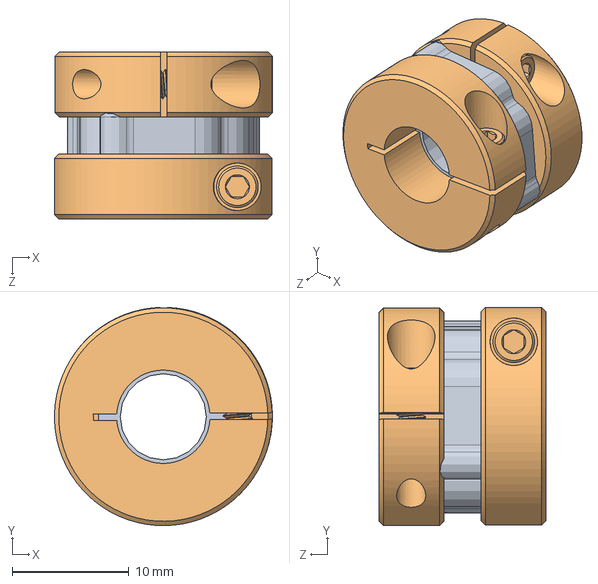
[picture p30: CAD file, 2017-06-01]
2.2 kN/CAD/v6 manufacturing/motor mount/coupling.SLDASM
18.7 x 18.7 x 14.3 mm
60635K860_HIGH-MISALIGNMENT FLEXIBLE SHAFT COUPLING
60635K103_HIGH-MISALIGNMENT FLEXIBLE SHAFT COUPLING x 2

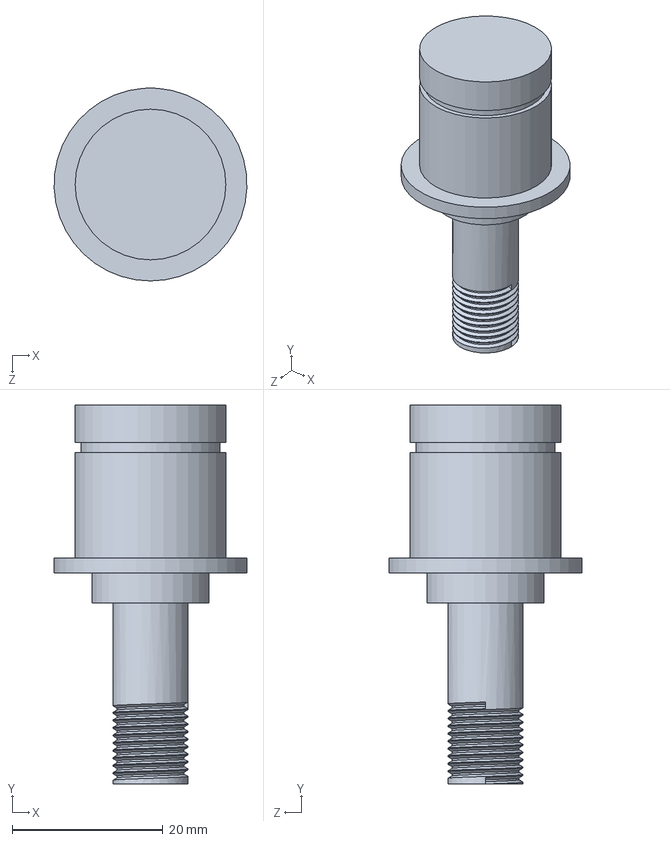
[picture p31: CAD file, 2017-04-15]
2.2 kN/CAD/v5/Bearing System/Shaft_Bearing System.SLDPRT
25.6 x 50.3 x 25.6 mm

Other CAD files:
2.2 kN/CAD/v6 manufacturing/assemblies/motor mount assembly v6.IGS
2.2 kN/CAD/v6 manufacturing/motor mount/Motor rest assembly.SLDASM
2.2 kN/CAD/v6 manufacturing/motor mount/Mirrored motor rest.SLDASM
2.2 kN/CAD/v5/bearing plate/bearing_plate_v3.SLDPRT
2.2 kN/CAD/Plumbing/3845K140_LIQUID-FILLED GAUGE.SLDPRT
2.2 kN/CAD/Plumbing/3846K351_MULTIPURPOSE GAUGE.SLDPRT
2.2 kN/CAD/Plumbing/4067T310_BRASS BALL VALVE W COMPRESSION TUBE FITTING.SLDPRT
2.2 kN/CAD/Plumbing/50785K228_MED-PRESSURE BRASS THREADED PIPE FITTING.SLDPRT
2.2 kN/CAD/Plumbing/50785K240_MED-PRESSURE BRASS THREADED PIPE FITTING.SLDPRT
2.2 kN/CAD/Plumbing/50785K337_MED-PRESSURE BRASS THREADED PIPE FITTING.SLDPRT
2.2 kN/CAD/Plumbing/50785K650_MED-PRESSURE BRASS THREADED PIPE FITTING.SLDPRT
2.2 kN/CAD/Plumbing/Aluminum_tubing 0.5_OD_0.38_ID_L3_in.SLDPRT
2.2 kN/CAD/Plumbing/Aluminum_tubing 0.5_OD_0.38_ID_L6_in.SLDPRT
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

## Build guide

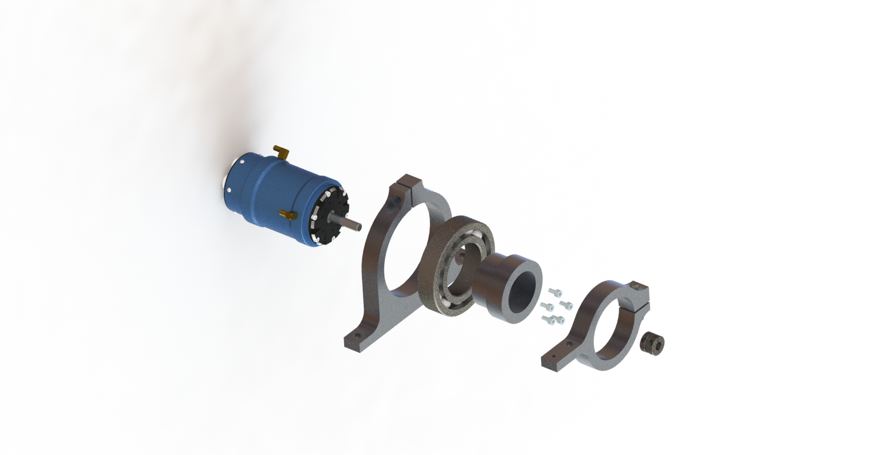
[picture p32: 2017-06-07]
Publicity/Photo/Exploded assembly of motor mount.JPG

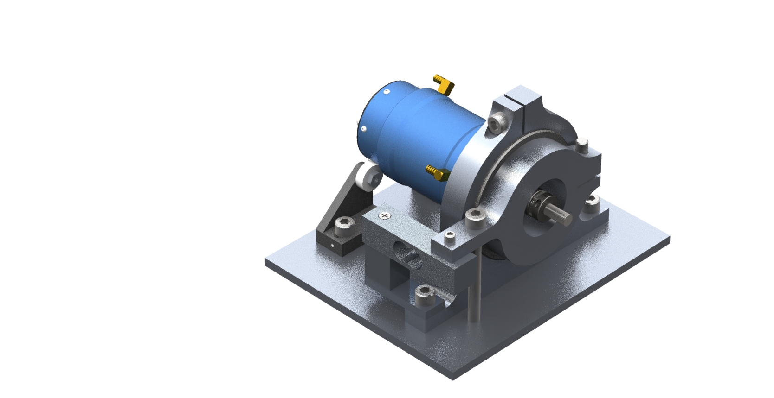
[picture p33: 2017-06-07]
Publicity/Photo/Motor mount assembly.JPG

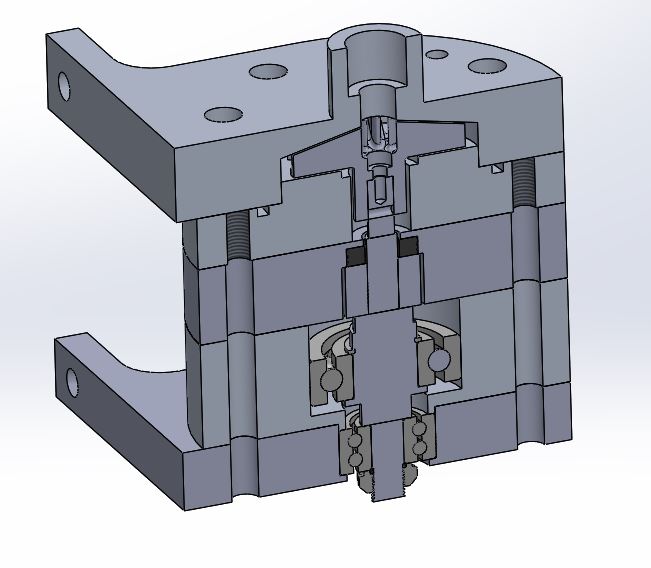
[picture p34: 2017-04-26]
Publicity/Photo/EFS_water_test_Assembly_cut.JPG

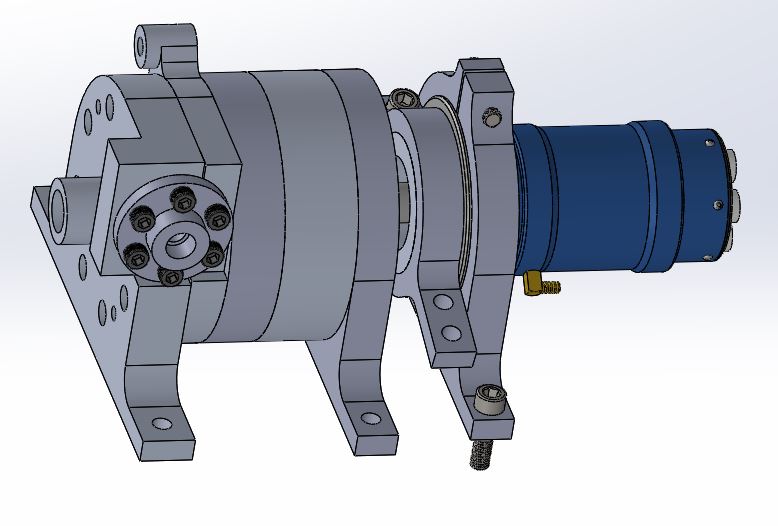
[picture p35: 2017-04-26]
Publicity/Photo/EFS_water_test_Assembly.JPG

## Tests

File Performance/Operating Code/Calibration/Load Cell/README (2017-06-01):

An HX711 load cell amplifer and generic load cell are used in the EFS torque load measurement system. Code and github attached in this folder are for the HX711 load cell amplifier.

The github page, where code and calibration instructions for the load cell and amplifier pair are located, can be found at: https://github.com/bogde/HX711

The code included in this folder is the calibration code, with the associated calibration factor found from calbration the load cell with known weights.

USEFUL LINKS:

HX711 purchase page - https://www.sparkfun.com/products/13879

HX711 Guide - https://learn.sparkfun.com/tutorials/load-cell-amplifier-hx711-breakout-hookup-guide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

Load Cell Basics - https://learn.sparkfun.com/tutorials/getting-started-with-load-cells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

Alternate github repo from sparkfun - https://github.com/sparkfun/HX711-Load-Cell-Amplifier/tree/V_1.1

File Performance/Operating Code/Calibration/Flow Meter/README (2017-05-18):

This file contains the circuit and code used to measure the rotational frequency on the Potter Aerospace Company turbine flow meter. The code and circuit can be used to calibrate cryogenic, and non-cryogenic fluids. Calibrate rotational frequency against known flowrates of your respective fluid. Calibrations are unique to the fluid and its properties (ie. LOX calibration will not give accurate flowrate measurements for water and vice versa).
Calibration curve for water will be made available here.

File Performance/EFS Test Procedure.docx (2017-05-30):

Electronic Propellant Feed System Centrifugal Pump Performance Test

This description of procedure defines the conditions for the hydraulic testing of the electric feed system centrifugal pump.

# Overview

The objectives of testing the electric feed systems centrifugal pump are to:

- Document system pump performance.
- Establish the system curve for the pumping system.
- Determine the operating point of the pump; i.e. the point where the pump’s impeller curve crosses the system curve with the discharge valve throttled and with the discharge valve fully open.
- Assess the match between “full flow”—flow delivered by the EFS pump with the discharge valve fully open—and the actual design flow requirement.
- Assess the implications of modifying pump performance via trimming the impeller, adding a cutwater, and using impellers of differing solidity.
- Detect and diagnose other control or performance problems.

Test Equipment

Pump suction and discharge pressures will be measured and recorded under each test condition. Pump pressures are measured using analog gauges and pre-calibrated pressure transducers on the pump inlet (suction side) and pump outlet (discharge side). A third transducer is tapped into the impeller housing. Fluid temperature at the pump inlet is recorded using a K-type thermocouple. Other useful equipment includes a load cell for measuring pump torque a tachometer and an amp/wattage probe.

## 1. EFS Pump Performance Testing

1.1 Verify all EFS pre-functional checklists are complete. Prior to performing any functional tests, the commissioning pre-start, start-up verification should be completed, Pre-functional checklist items include, but are not limited to, the following:

1.1.1 Control system point-to-point checkout is completed to ensure all EFS input/output points are wired correctly, and all actuators and relays or motor starters respond to control signals.

1.1.2 Power is provided to pump assembly at proper voltage and phase rotation. As an alternative to verifying phase rotation, pump rotation should be verified.

1.1.3 The electric feed system has been proportionally balanced with all control valves fully open.

1.1.4 All necessary sensors are calibrated.

1.1.5 Locations of EFS pump, valves, and other system components are clearly and correctly located on as-built drawings.

# EFS Standard Operating Procedure

## Preliminaries

1. With discharge valve closed, suction valve of the pump is opened which causes fluid flow to the impeller and fills the volute.
2. Open the vent (drain) valve which is on the discharge line before the discharge valve of the pump which will cause all air to move out of the casing and flow loop.
3. When some quantity of the fluid exits from the vent valve close it.
4. The pump discharge and suction valves are adjusted to the fully open position and the motor speed set to zero.
5. The electrical supply and motor drive switch are turned on. The motor control knob is adjusted slowly to [insert]. The system is ensured to have no leaking. All the gauges etc. are checked to reduce the motor speed back to zero.

## Test Process

1. Suction valve and discharge valve is fully open. The maximum speed N (rpm) is selected by adjusting speed control to [insert] %.
2. Discharge valve is fully opened and water is allowed to circulate. The volume of flow indicator is noted and decides suitable increments in flow to give adequate sample points.
3. Allow the pump to attain its capacity read from the discharge line pressure gauge. When the readings are stable, record all test measurements.
4. The discharge valve is then slowly adjusted (decreasing flow) to the next desired capacity point.
5. Step 4 is repeated until all flow increments have been recorded.
6. All the gauges etc. are checked to reduce the motor speed back to zero and power down the EFS system.

Test Precautions

- Exercise care when changing operating RPM if the equipment served by the pump is in operation.
- Avoid sudden flow changes to minimize the potential for water hammer, especially when throttling the discharge valve for a shut-off test.
- Verify that all components between the discharge of the pump and the discharge throttling valve (including the pump casing) are rated for the peak pressure with the impeller installed plus the static pressure on the inlet side of the pump prior to performing a shutoff test.
- Exercise proper caution when working around live wiring and terminals and taking voltage or amp readings.
- Exercise proper caution while working around the rotating parts of the pump.
- DO NOT let EFS centrifugal pump operate for long periods of time at zero flow.
- DO NOT operate pump in reverse direction, this could cause severe damage to the impeller shaft.
- DO NOT run EFS pump dry.

## 2. Analysis and Opportunities

2.1 Analyze data. After conducting the tests, the recorded data will be used to assess the pump’s performance. The operation of the system will always occur at the point where the pump curve (which is concretely defined for the EFS pump by the impeller and the pump rotational speed) intersects the system curve (which will change depending on the operating mode). If the pump is producing flow greater than necessary, changing either the pump impeller size or the pump speed can deliver design flow at reduced power.

2.1.1 Determine the actual impeller size by plotting no-flow pressure on the set of pump curves produced through testing. Keep in mind that measurement errors will influence the calculated differential pressure across the pump.

2.1.2 Plot the wide-open operating point by following the pump curve for each impeller to the pressure reading from the worst-case wide-open test. Note the flow rate at this point. This point defines the system curve for the system with the discharge valve wide open.

2.1.3 Use the worst-case wide-open point on the pump curve to manually draw in the system curve on the set of pump curves. Use the following equation to determine approximate points for a range of intermediary flow rates on the system curve:

Hintermediary = Hmin + [Hwide-open × (Qintermediary / Qwide-open)²]

Where, H, is head, Q, is flow, and Hmin refers to the minimum pressure requirement for the system. The system curve will cross the “head” axis at the minimum pressure value when flow is 0 GPM.

2.1.4 Identify on the system curve the operating point achievable with an impeller trim or speed change: the point on the system curve that corresponds to the design flow rate.

2.1.5 Locations of EFS pump, valves, and other system components are clearly and correctly located on as-built drawings.

2.2 Estimate energy use.

System brake horsepower can be estimated from the pump curves or calculated using the following equation:

bhp = [flow × head] / [3960 × pump efficiency]

Where flow is in gallons per minute, head is in feet, and pump efficiency is read off the pump curve.

Motor input power is calculated by:

kW = [bhp × 0.746 kW/hp] / motor efficiency

Where motor efficiency can be estimated based on motor rated efficiency and part load operating point.

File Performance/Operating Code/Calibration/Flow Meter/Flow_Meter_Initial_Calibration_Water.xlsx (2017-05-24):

Analog Read | Flowrate (lpm) | Flowrate (gpm)
568 | 0 | 0
676 | 5.21 | 1.37633612
682 | 6.26 | 1.65371672
692 | 7.37 | 1.94694764
697 | 8.1 | 2.1397932
701 | 8.35 | 2.2058362
705 | 8.82 | 2.32999704
709 | 9.27 | 2.44887444
 |  | 0
 |  | 0
 |  | 0
 |  | 0
 |  | 0
 |  | 0
 |  | 0
 |  | 0
 |  | 0
 |  | 0
 |  | 0
12.49601072

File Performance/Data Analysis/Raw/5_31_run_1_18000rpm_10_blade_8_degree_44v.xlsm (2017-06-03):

Date | Time | millis | RPM | Load | Torque(in-lbs) | pIN | pOUT
2017-05-31 | 11:56:17 | 1924 | 0 | 0 | 0 | 0 | 0
2017-05-31 | 11:56:17 | 2155 | 0 | 0 | 0 | 0.97 | 0
2017-05-31 | 11:56:18 | 2414 | 0 | 0 | 0 | 0.97 | 0
2017-05-31 | 11:56:18 | 2672 | 0 | 0 | 0 | 0.97 | 0
2017-05-31 | 11:56:18 | 2931 | 0 | 0 | 0 | 0.97 | 0
2017-05-31 | 11:56:18 | 3189 | 0 | 0 | 0 | 0.97 | 0
2017-05-31 | 11:56:19 | 3448 | 0 | 0 | 0 | 0.97 | 0
2017-05-31 | 11:56:19 | 3707 | 0 | 0 | 0 | 0.97 | 0
2017-05-31 | 11:56:19 | 3965 | 0 | 0 | 0 | 0.97 | 0
2017-05-31 | 11:56:19 | 4225 | 0 | 0 | 0 | 0.97 | 0
2017-05-31 | 11:56:20 | 4483 | 0 | 0 | 0 | 0.97 | 0
2017-05-31 | 11:56:20 | 4742 | 0 | 0 | 0 | 0.97 | 0
2017-05-31 | 11:56:20 | 5001 | 0 | 0 | 0 | 0.97 | 0
2017-05-31 | 11:56:20 | 5259 | 0 | 0 | 0 | 0.97 | 0
2017-05-31 | 11:56:21 | 5518 | 0 | 0 | 0 | 0.97 | 0
2017-05-31 | 11:56:21 | 5777 | 0 | 0 | 0 | 0.97 | 0
2017-05-31 | 11:56:21 | 6035 | 0 | 0 | 0 | 0.97 | 0
2017-05-31 | 11:56:21 | 6294 | 0 | 0 | 0 | 0.97 | 0
2017-05-31 | 11:56:22 | 6552 | 0 | 0 | 0 | 0.06 | 0
2017-05-31 | 11:56:22 | 6811 | 0 | 0 | 0 | 0.97 | 0
2017-05-31 | 11:56:22 | 7070 | 0 | 0 | 0 | 0.97 | 0
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

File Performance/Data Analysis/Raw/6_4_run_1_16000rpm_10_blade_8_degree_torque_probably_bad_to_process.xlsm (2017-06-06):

Date | Time | millis | RPM | Load | Torque(in-lbs) | pIN | pC | pOUT | Qgpm _ too high | flow meter RPM (derived) | Qgpm corrected | diffuser rise
2017-06-04 | 13:17:55 | 1924 | 0 | 0 | 0 | 0 | 0 | 0 | 0
2017-06-04 | 13:17:55 | 2154 | 0 | 0 | 0.22 | 0 | 0 | 0 | 0
2017-06-04 | 13:17:55 | 2413 | 0 | 0 | 0.05 | 0 | 0 | 0 | 0
2017-06-04 | 13:17:56 | 2671 | 0 | 0 | 0.04 | 0 | 0 | 0 | 0
2017-06-04 | 13:17:56 | 2930 | 0 | 0 | 0.02 | 0 | 0 | 0 | 0
2017-06-04 | 13:17:56 | 3188 | 0 | 0 | 0 | 0.09 | 0 | 0 | 0
2017-06-04 | 13:17:56 | 3447 | 0 | 0 | 0 | 0.09 | 0 | 0.44 | 0
2017-06-04 | 13:17:57 | 3705 | 0 | 0 | 0 | 0.09 | 0 | 0.44 | 0
2017-06-04 | 13:17:57 | 3964 | 0 | 0 | 0 | 0 | 0 | 0 | 0
2017-06-04 | 13:17:57 | 4222 | 0 | 0 | 0 | 0 | 0 | 0 | 0
2017-06-04 | 13:17:57 | 4482 | 0 | 0 | 0.01 | 5.13 | 2.61 | 0.44 | 0
2017-06-04 | 13:17:58 | 4740 | 0 | 0 | 0 | 88.19 | 87.35 | 89.29 | 0
2017-06-04 | 13:17:58 | 4999 | 0 | 0 | 0 | 88.19 | 88.19 | 89.29 | 0
2017-06-04 | 13:17:58 | 5257 | 0 | 0 | 0 | 88.19 | 88.19 | 89.29 | 0
2017-06-04 | 13:17:58 | 5516 | 0 | 0 | 0 | 88.19 | 88.19 | 89.29 | 0
2017-06-04 | 13:17:59 | 5774 | 0 | 0 | 0 | 89.03 | 88.19 | 89.29 | 0
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

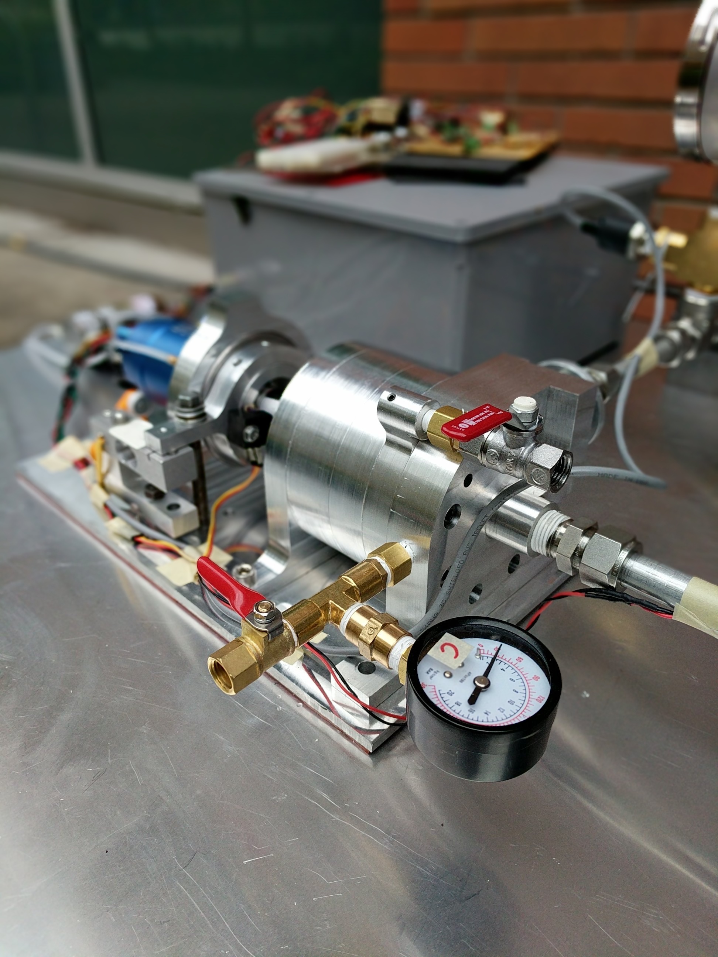
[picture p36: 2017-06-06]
Publicity/Photo/testing photo (7).jpg

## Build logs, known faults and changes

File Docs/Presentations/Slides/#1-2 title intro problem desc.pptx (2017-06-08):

## PSAS Electric Propellant Feed System

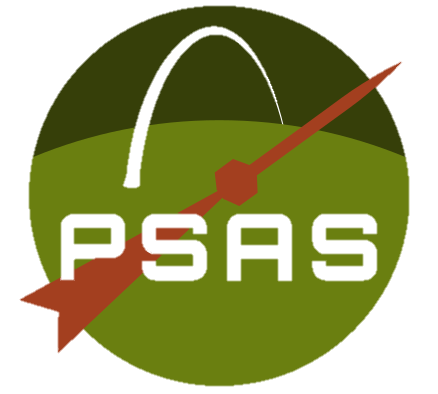
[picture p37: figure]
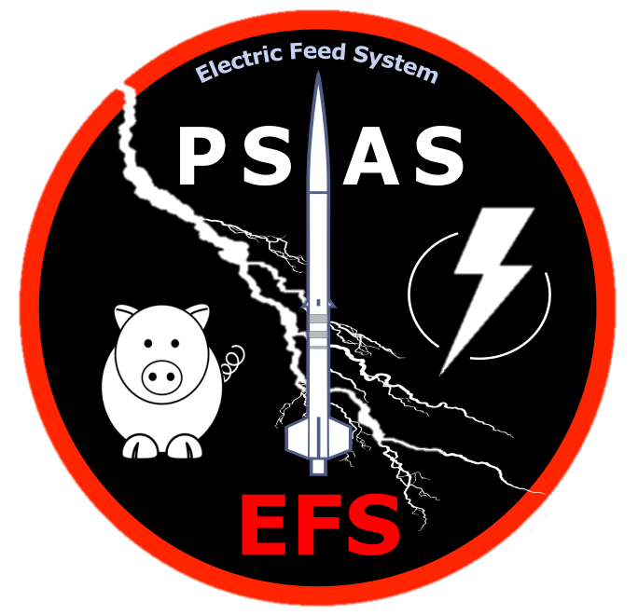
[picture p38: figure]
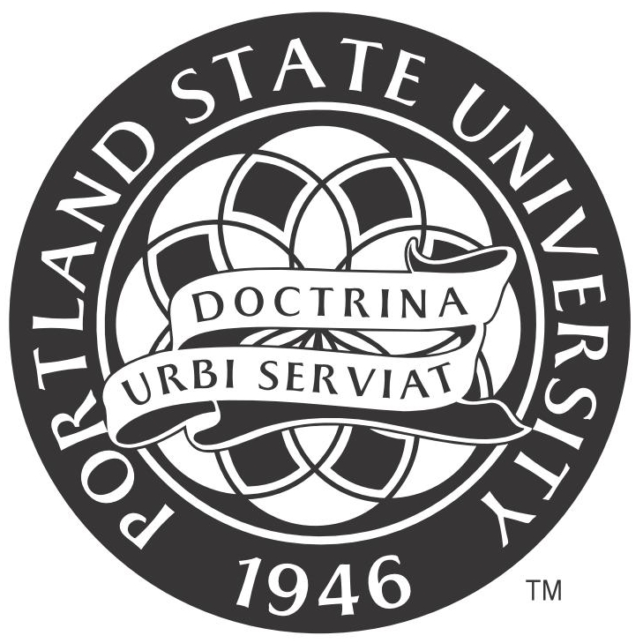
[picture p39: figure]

Affiliations: ¹Portland State Aerospace Society, ²Maseeh College of Engineering and Computer Science Portland, OR, 97201, United States

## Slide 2

The Team

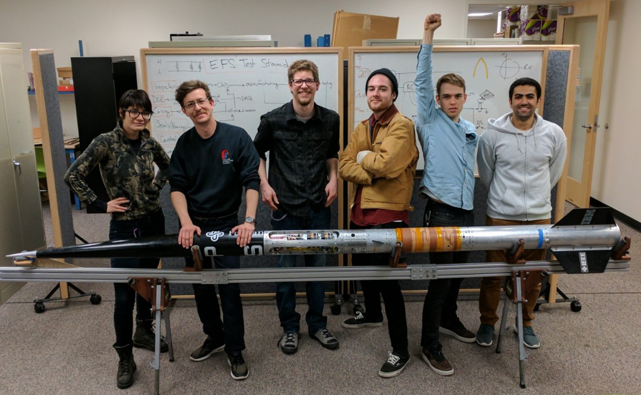
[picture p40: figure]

Team Members (left to right):
Mimi Shang, James Luce, Jorden Roland, Johnny Froehlich, Johnathan Talik, Rawand Rasheed

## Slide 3

The Problem

Portland State Aerospace Society (PSAS) wants its rockets to go higher, but mass is the enemy:

Δv = change in velocity
Ve = exhaust velocity
mo = mass of rocket + propellant
mf = mass of rocket

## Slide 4

Past approach: solid propellant

- Most small rockets use solid propellant.
- Simple but inefficient.
- Can’t throttle = can’t insert into orbit.

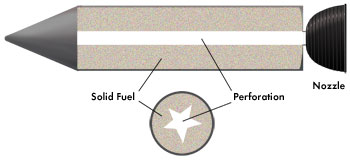
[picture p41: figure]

Solid propellant rocket design

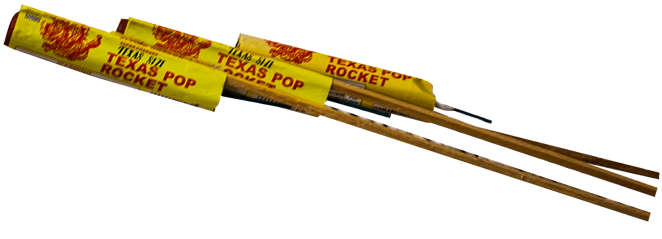
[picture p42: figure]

Solid propellant rocket example

Solid propellant

Grain bore

Nozzle

Images: http://www.fireworkssupermarket.com, http://www.aerospace.org

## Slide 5

Liquid propellant

- Gives more Δv for its mass = goes higher.
- Can be throttled = can insert into orbit.

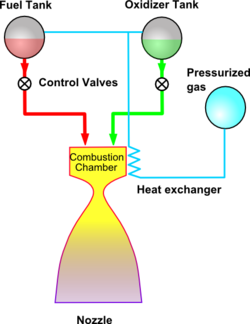
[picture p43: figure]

Pressure fed: too heavy

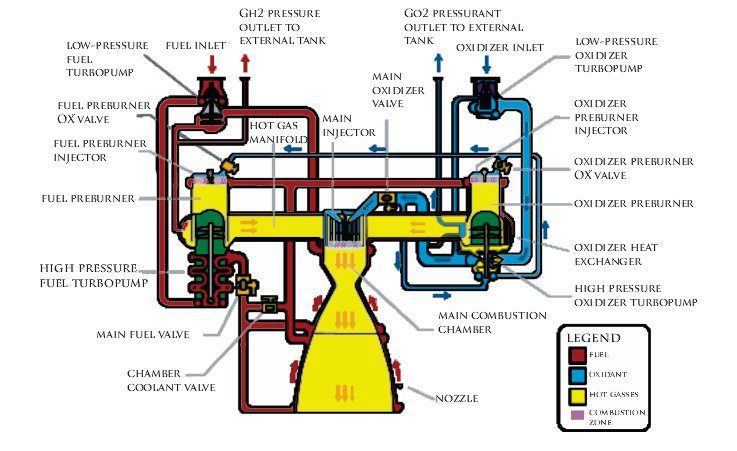
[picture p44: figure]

Turbopump: too complex

Images from wikipedia

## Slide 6

New approach: electric pump

- Turbopump without turbine = just a pump.
- Battery energy density has been rising.
- Lighter than pressure fed, simpler than turbopump.

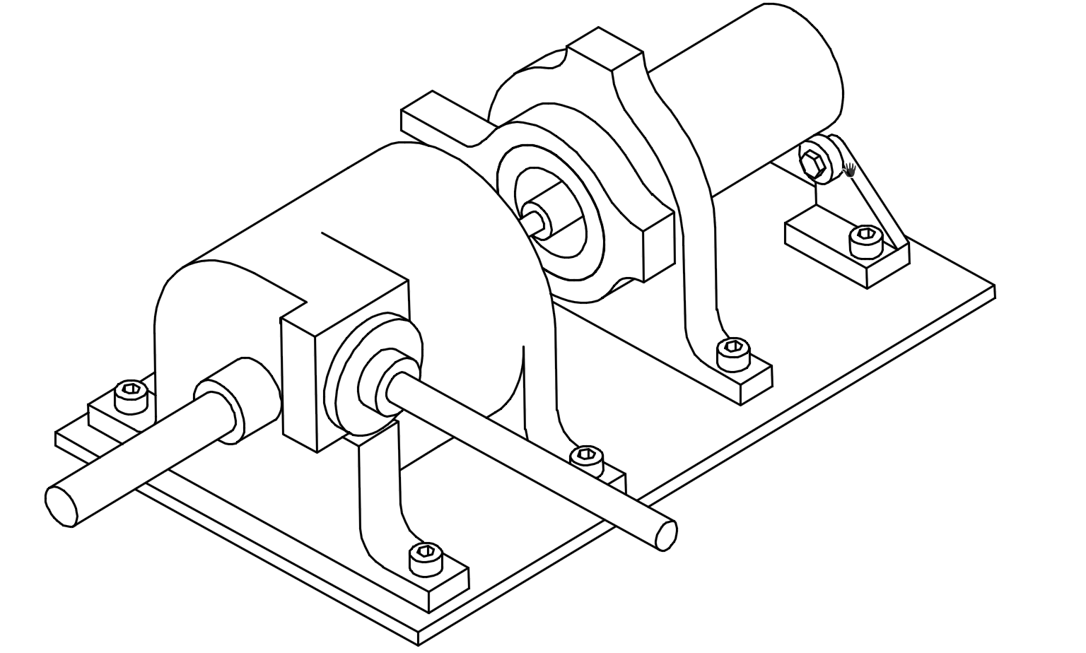
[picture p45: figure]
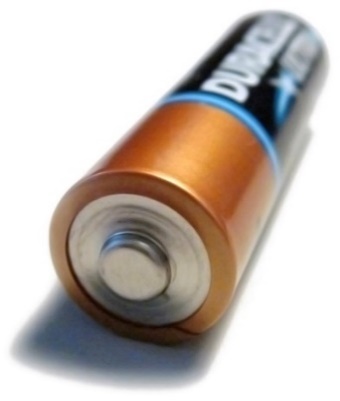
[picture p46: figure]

Pump

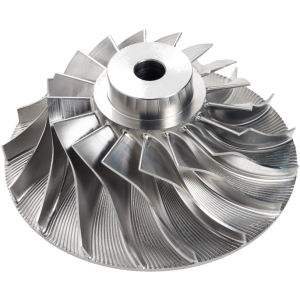
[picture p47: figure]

Engine

Electric motor

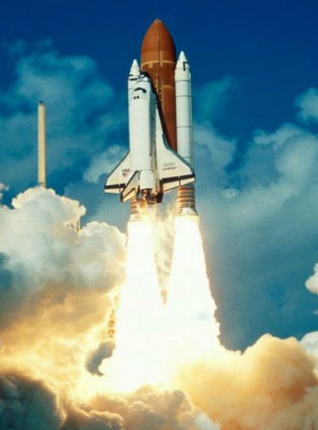
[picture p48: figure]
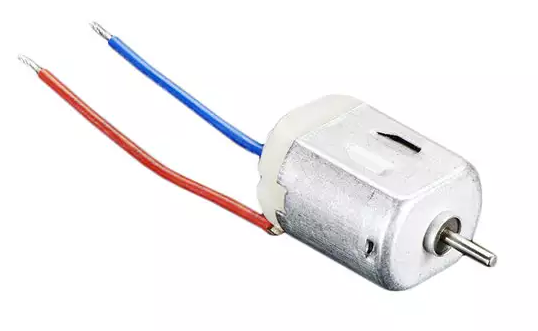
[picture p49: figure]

Tank

https://en.wikipedia.org/
http://www.blue-sky-technologies.com/impeller-seal-repair/
https://www.digikey.com/

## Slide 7

Project Goal

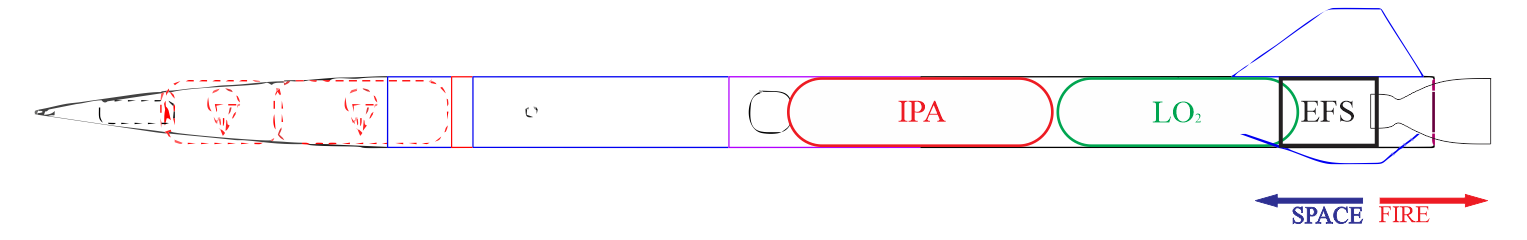
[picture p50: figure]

Goal:
- Design a test pump to meet PSAS’ requirements.
- Test with water (not cryogenic liquid oxygen and isopropyl alcohol).
- Performance results will be scaled to design actual rocket pump.

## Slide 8

Customer Requirements

Pressure delivery | Must produce discharge pressures of 300-400 psi.
Flow capacity | Must supply a flow rate of ~12 gpm.
Transferability | Documentation must be open source and transferable to future PSAS engineers.
Off-the-shelf components | Must utilize off the shelf components wherever possible.
Cost | Project must be completed for less than $8000

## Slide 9

Customer Requirements

Open-ended literature review

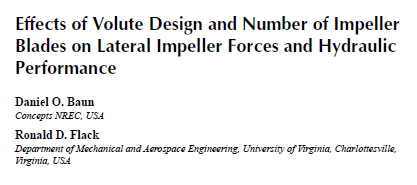
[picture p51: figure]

Math is involved

Scientific computing

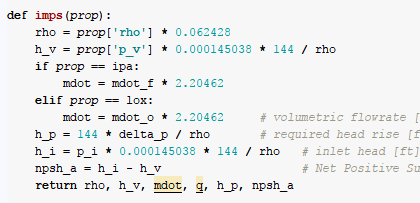
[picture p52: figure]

Some
assumptions

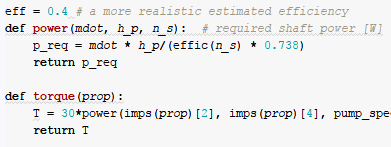
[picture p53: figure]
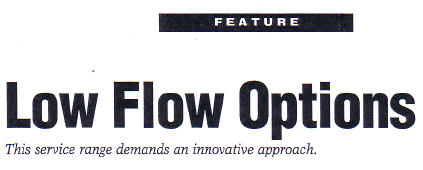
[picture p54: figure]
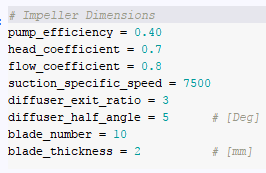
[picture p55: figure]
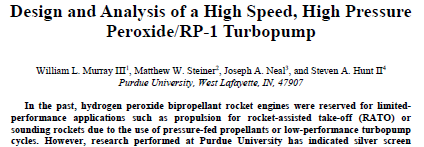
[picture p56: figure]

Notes: literature review to narrow the region of interest. (Don’t solve problems we don’t have to)

Scientific computing as an example of using tools to implement theory OR IDEAS. Matercam, SW, Python, Arduino

Allows us to make calculations (OR DESIGNS) over a wide range of values and explore a little.
We can iteratively develop

note:

Guessing is cheaper

If best head coeff is between 0.5 and 1 we use 0.75

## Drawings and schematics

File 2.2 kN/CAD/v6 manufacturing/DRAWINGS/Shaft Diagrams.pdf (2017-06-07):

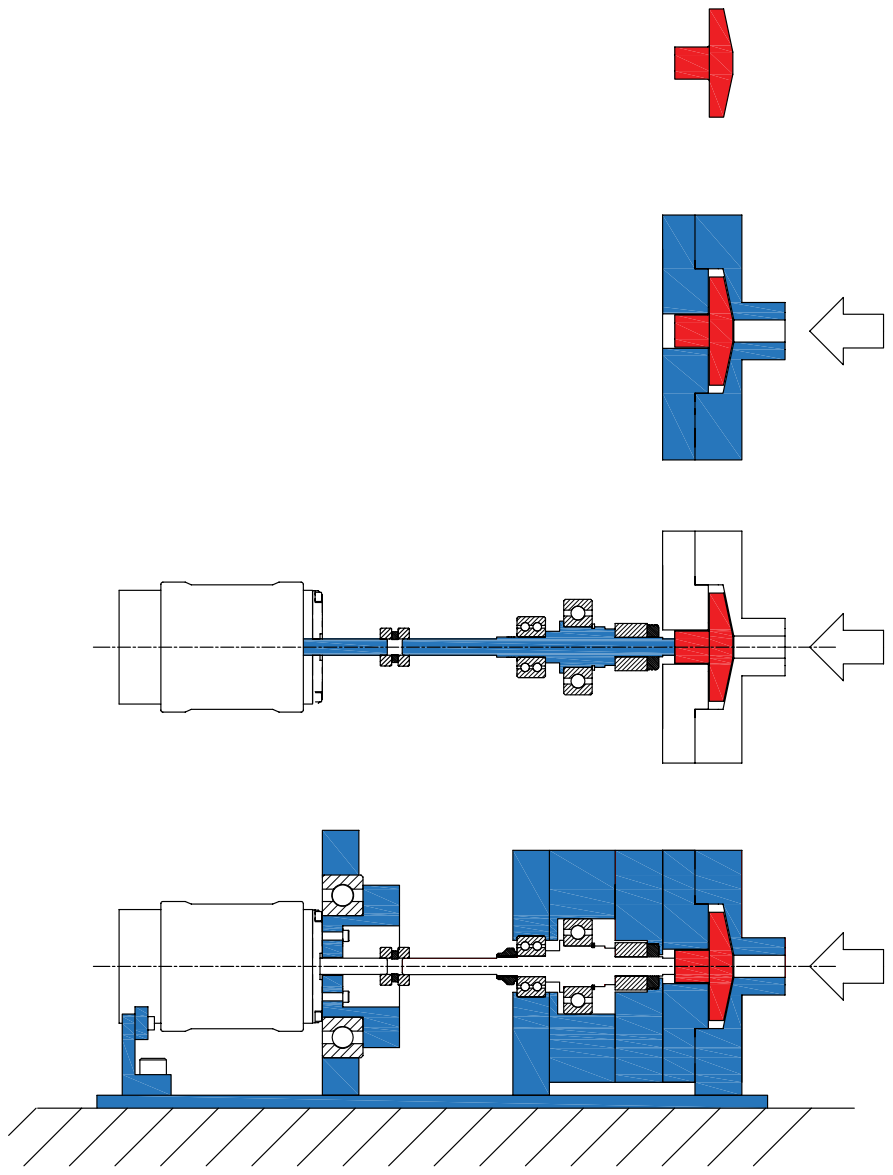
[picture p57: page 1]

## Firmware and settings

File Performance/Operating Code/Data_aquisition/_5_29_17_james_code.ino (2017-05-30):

//5/29/17 - confirmed working functions: 
//- motor control via digital pot
//- RPM reading 
//- torque reading
//- LCD output of motor load, rpm, torque
//- PLX-DAQ excel output of time, load, rpm, torque
//Should work but needs to be validated:
//-pressure transducers.

//--------load cell--------//

#include "HX711.h"
#define DOUT  8
#define CLK  9
HX711 scale(DOUT, CLK);
float calibration_factor = -117500; //-117500.00 seems to work well

float load_cell_lbs = 0;
float torque_arm = 3; // length of torque arm in inches, needs to be checked
float torque = 0;     //torque in inch-lbs

//--------LCD--------//

#include <Wire.h>  
#include <LiquidCrystal_I2C.h> // Using version 1.2.1
LiquidCrystal_I2C lcd(0x27, 2, 1, 0, 4, 5, 6, 7, 3, POSITIVE); 
int load=0; 
int LCDrate = 100;                      //number of millis between LCD refresh
unsigned long LCDlastRefresh;
int serialPrintRate = 200;              //number of millis between serial prints refresh
unsigned long serialPrintLastRefresh;

//--------programmable pot--------//

#include <SPI.h>
byte potAddress = 0x00;
int CS= 4;
unsigned long potWriteValue = 0L;

//--------input pot--------//

const int numPotReadings = 5;      // pot reading: number of readings for smoothing
int potReadings[numPotReadings];   // pot reading: the readings from the analog input
int potReadIndex = 0;              // pot reading: the index of the current reading
int potTotal = 0;                  // pot reading: the running total
int potAverage = 0;                // pot reading: the average
int potInputPin = A0;
unsigned long potRounded = 0;
int potPreRounded = 0;
int potRoundingLevel = 20;         // this is the size of the step of pot readings (1 means 1023 levels, 20 means 1023/20 levels)

//--------RPM reading--------//

volatile byte half_revolutions;
unsigned long rpm;
unsigned long timeold;
unsigned long lastRPM;
unsigned long maxRPM=0;

//--------pressure reading--------//
int pIN_read=0;
float pIN=0;
int pINinputPin = A2;
int pOUT_read=0;
float pOUT=0;
int pOUTinputPin = A3;
int pC_read=0;
float pC=0;
int pCinputPin = A4;

//------------------------setup------------------------//
 
void setup()
{
 Serial.begin(9600);
 Serial.println("CLEARDATA");  //for excel
 Serial.println("LABEL,Date,Time,millis,RPM,Load,Torque(in-lbs),pIN,pOUT");  //LABEL command creates label for columns in the first row with bold font

//--------load cell--------//

  Serial.println("HX711 calibration sketch");
  Serial.println("Remove all weight from scale");
  Serial.println("After readings begin, place known weight on scale");
  Serial.println("Press + or a to increase calibration factor");
  Serial.println("Press - or z to decrease calibration factor");

  scale.set_scale();
  scale.tare(); //Reset the scale to 0
  long zero_factor = scale.read_average(); //Get a baseline reading
  
  Serial.print("Zero factor: "); //This can be used to remove the need to tare the scale. Useful in permanent scale projects.
  Serial.println(zero_factor);

//--------RPM reading setup--------//

 attachInterrupt(1, rpm_fun, RISING);
 half_revolutions = 0;
 rpm = 0;
 timeold = 0;
 lastRPM = millis();

//--------LCD setup--------//
   
 lcd.begin(20,4); // sixteen characters across - 4 lines
 lcd.backlight();
   
//--------programmable pot setup--------//

 pinMode (CS, OUTPUT);
 SPI.begin();

//--------input pot setup--------//

 for (int potReading = 0; potReading < numPotReadings; potReading++) 
      {potReadings[potReading] = 0;}

//------------------------Loop------------------------//

}
void loop()
{

//--------serial print--------//

if (millis() > serialPrintLastRefresh + serialPrintRate) 
    {
      serialPrintLastRefresh=millis();
      
      Serial.println( (String) "DATA,DATE,TIME," + millis() + "," + rpm + "," + load + "," + torque + "," + pIN + "," + pOUT);
      
     // Serial.print("millis ");
     // Serial.print(millis());
     // Serial.print(" RPM ");
     // Serial.print(rpm);
     // Serial.print(" load ");
     // Serial.print(load);
     // Serial.print(" digipot_pos ");
     // Serial.println(potWriteValue);
    }

//--------LCD print--------//

  if (millis() > LCDlastRefresh + LCDrate) 
    {
      LCDlastRefresh=millis();

      lcd.setCursor(0,0);
      lcd.print("RPM ");
      lcd.setCursor(4,0);
      lcd.print(rpm);
      
      lcd.setCursor(10,0);
      lcd.print("motor ");
      lcd.setCursor(16,0);
      lcd.print(load);
    
      if(load < 10) 
        {
          lcd.setCursor(17,0);
          lcd.print("  ");  
        }
      if(load > 10 && load < 100) 
        {
          lcd.setCursor(18,0);
          lcd.print(" ");  
        }

      lcd.setCursor(0,1);
      lcd.print("t(inlbs) ");
      lcd.setCursor(9,1);
      lcd.print(torque);
      
      lcd.setCursor(0,2);
      lcd.print("pIN ");
      lcd.setCursor(4,2);
      lcd.print(pIN,0);

      lcd.setCursor(8,2);
      lcd.print("pOUT ");
      lcd.setCursor(13,2);
      lcd.print(pOUT,0);
      
      lcd.setCursor(0,3);
      lcd.print("time ");
      lcd.setCursor(5,3);
      lcd.print(millis()/1000);       
    }

//--------Pressure transducers--------//

  pIN_read=analogRead(pINinputPin);
  pIN=0.9123*pIN_read-130.4;
  if (pIN < 0) 
    {
      pIN=0;
    }

  pOUT_read=analogRead(pOUTinputPin);
  pOUT=0.00121*pOUT_read+1;
 if (pOUT < 0) 
  {
    pOUT=0;
  }
    
//--------Load cell--------//

  scale.set_scale(calibration_factor); //Adjust to this calibration factor

  load_cell_lbs = -scale.get_units()-.02;
  if (load_cell_lbs < 0)
    {
      load_cell_lbs=0;
    }
  torque = torque_arm*load_cell_lbs;

  //Serial.print("Reading: ");
  //Serial.print(scale.get_units(), 2);
  //Serial.print(" lbs"); //Change this to kg and re-adjust the calibration factor if you follow SI units like a sane person
  //Serial.print(" calibration_factor: ");
  //Serial.print(calibration_factor);
  //Serial.println();

  //if(Serial.available())
  //{
  //  char temp = Serial.read();
  //  if(temp == '+' || temp == 'a')
  //    calibration_factor += 10000;
  //  else if(temp == '-' || temp == 'z')
  //    calibration_factor -= 10000;
  //}

//--------RPM reading--------//
    
  if (rpm > 0) 
    {                                              //this makes sure that if it's not spinning the RPM returns to zero on the LCD 
       if (lastRPM <= (millis()-1000)) 
       {
         rpm=0;
       }
    }
  
  if (half_revolutions >= 20)                     //Update RPM every 20 counts, increase this for better RPM resolutio
   {                               
     rpm = 30*1000/(millis() - timeold)*half_revolutions;
     rpm=2*rpm;
     timeold = millis();
     half_revolutions = 0;

     if (rpm > maxRPM) 
      {
        maxRPM=rpm;
      }
   }

//--------pot reading and smoothing--------//

  potTotal = potTotal - potReadings[potReadIndex];          // subtract the last reading
  potReadings[potReadIndex] = analogRead(potInputPin);      // read from the sensor
  potTotal = potTotal + potReadings[potReadIndex];          // add the reading to the total
  potReadIndex = potReadIndex + 1;                          // advance to the next position in the array

  if (potReadIndex >= numPotReadings) {                // if we're at the end of the array...
    potReadIndex = 0;                                  // ...wrap around to the beginning
  }

  potAverage = potTotal / numPotReadings;      // calculate the average
  potPreRounded = potAverage/potRoundingLevel;
  potRounded =  potPreRounded*potRoundingLevel;                             

//--------writing to digital pot--------//

  potWriteValue = map(potRounded,20,1020,0,110);
  if (potWriteValue > 200) 
    {
       potWriteValue = 0;
    }
  if (potWriteValue > 128) 
    {
       potWriteValue = 128;
    }
  digitalPotWrite(potWriteValue);
  load = map(potWriteValue,0,110,0,100);
}  

//--------functions--------//

void rpm_fun() //Each rotation, this interrupt function is run twice
  {
    half_revolutions++;
    lastRPM=millis();
  }

int digitalPotWrite(int Value)
  {
    digitalWrite(CS, LOW);
    SPI.transfer(potAddress);
    SPI.transfer(potWriteValue);
    digitalWrite(CS, HIGH);
  }

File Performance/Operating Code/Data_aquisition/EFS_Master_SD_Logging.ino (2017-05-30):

/*
 The circuit:
 * analog sensors on analog ins 0, 1, and 2
 * SD card attached to SPI bus as follows:
 ** MOSI - pin 11
 ** MISO - pin 12
 ** CLK - pin 13
 ** CS - pin 4 (for MKRZero SD: SDCARD_SS_PIN)
 */

#include <SPI.h>
#include <SD.h>
const int chipSelect = 4;
#include "Adafruit_MAX31855.h"
#include <Servo.h>


#define MAXDO   3
#define MAXCS   4
#define MAXCLK  5

Servo myservo;

// initialize the Thermocouple
Adafruit_MAX31855 thermocouple(MAXCLK, MAXCS, MAXDO);

int pt1=A0;
int pt2=A1;
int flow_m=A2;

unsigned long t_time_update=0;

void setup() {
  Serial.begin(9600);
  while (!Serial) {
    ;
  }

  Serial.print("Initializing SD card...");

  if (!SD.begin(chipSelect)) {
    Serial.println("Card failed, or not present");
    return;
  }
  Serial.println("card initialized.");
  myservo.attach(9);
  File dataFile = SD.open("datalog.txt", FILE_WRITE);
  dataFile.print("PT1 (Psi)");
  dataFile.print("          ");
  dataFile.print("PT2 (Psi)");
  dataFile.print("        ");
  dataFile.print("TC (Celsius)");
  dataFile.print("       ");
  dataFile.println("Flow (Gpm)");
  dataFile.close();

  Serial.print("PT1 (Psi)");
  Serial.print("     ");
  Serial.print("PT2 (Psi)");
  Serial.print("     ");
  Serial.print("TC (Celsius)");
  Serial.print("     ");
  Serial.println("Flow (Gpm)");
  
  delay(500);
}

void loop() {
 float pt_1, pt_2, flowm;
 unsigned long t_time=millis();
 
 if(t_time - t_time_update < 250){
//Thermocouple ..........................................................
  //Serial.print("Internal Temp = ");
  //Serial.println(thermocouple.readInternal());
  float c = thermocouple.readCelsius();
   if (isnan(c)) {
     //Serial.println("Something wrong with thermocouple!");
   } else {
     //Serial.print("C = "); 
     //Serial.println(c);
   }
   //Serial.print("F = ");
   //Serial.println(thermocouple.readFarenheit());
   
// Pressure Transducer..........................................................
 pt_1 = analogRead(pt1);
 //Serial.print(pt1);

 pt_2=analogRead(pt2);
 //Serial.print(pt1);

 flowm=analogRead(flow_m);
 //Serial.print(pt1);

 // make a string for assembling the data to log:
  String dataString = "";
  dataString += String(pt_1);
  
  String dataString1 = "";
  dataString1 += String(pt_2);

  String dataString2 = "";
  dataString2 += String(thermocouple.readCelsius());

  String dataString3 = "";
  dataString3 += String(flowm);
  

  // open the file. note that only one file can be open at a time,
  // so you have to close this one before opening another.
  File dataFile = SD.open("datalog.txt", FILE_WRITE);

  // if the file is available, write to it:
  if (dataFile) {
    dataFile.print(dataString);
    dataFile.print("              ");
    dataFile.print(dataString1);
    dataFile.print("             ");
    dataFile.print(dataString2);
    dataFile.print("             ");
    dataFile.println(dataString3);
    dataFile.close();
    // print to the serial port too:
    Serial.print(dataString);
    Serial.print("              ");
    Serial.print(dataString1);
    Serial.print("             ");
    Serial.print(dataString2);
    Serial.print("             ");
    Serial.println(dataString3);
  }
  // if the file isn't open, pop up an error:
  else {
    Serial.println("error opening datalog.txt");
  }
 
   }
 if (t_time - t_time_update >= 400){
  t_time_update=t_time;
 }
  
  
}

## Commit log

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2017-02-11 - Updated propellant properties - Added water properties to dictionary - Misc formatting fixes
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2017-02-23 added CAD folder with dumb impeller
    [Impeller_v1.0.SLDPRT]
2017-03-01 made cad of our motor
    [91251A243_BLACK-OXIDE ALLOY STEEL SOCKET HEAD CAP SCREW.SLDPRT, 91255A075_ALLOY STEEL BUTTON-HEAD SOCKET CAP SCREW.SLDPRT, Aquastarr_T20.SLDASM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]
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2017-03-05 correct bolt size on motor casing
    [Cap.SLDPRT]
2017-03-30 Add files via upload
    new bearing dimensions
    [bearing_JL_3_5_17.SLDPRT]
2017-03-30 Add files via upload
    new shaft design for thrust loading
    [impeller_shaft_JL_3_13_17.SLDPRT]
2017-03-30 Add files via upload
    bearing retaining plate
    [bearing_plate_JL_3_14_17.SLDPRT]
2017-03-30 Add files via upload
    big seal (contacts impeller)
    [big_seal_JL_3_14_17.SLDPRT]
2017-03-30 Add files via upload
    rigid shaft coupling https://www.mcmaster.com/#5395T212
    [5395T212_SET SCREW RIGID SHAFT COUPLING.SLDPRT, coupler_shaft_JL_3_13_17.SLDPRT]
2017-03-30 Add files via upload
    various fasteners from assembly
    [M4x8.SLDPRT, TORNILLO DIN-912-2014.SLDPRT, m4_button_head_edit.SLDPRT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]
2017-03-30 Add files via upload
    newer impeller model, more robust
    [impeller_parameterized_JL_3_13_17.SLDPRT]
2017-03-30 Add files via upload
    new assembly (motor not included for computing efficiency)
    [water_test_assembly_JL_3_14_17.SLDASM]
2017-03-30 Add files via upload
    just updated dowel
    [impeller_dowel.SLDPRT]
2017-03-30 Add files via upload
    the all important housing
    [impeller_housing_v2_JL_3_16_17.SLDPRT, impeller_housing_v3_JL_3_28_17.SLDPRT]
2017-03-30 Add files via upload
    updated motor mount design
    [motor mount_JL__v2_3_29_17.SLDPRT]
2017-03-30 Add files via upload
    upper and lower seal retaining plates
    [big_seal_plate_JL_3_14_17.SLDPRT, small_seal_plate_JL_3_14_17.SLDPRT]
2017-03-30 Add files via upload
    smaller (main) seal
    [seal_JL_3_5_17.SLDPRT]
2017-03-31 Add files via upload
    diffuser length and fittings added
    [impeller_housing_v3_JL_3_28_17.SLDPRT]
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2017-04-06 uploading v4 EFS cad drawings
    [1_8 OD tubing fitting 50715K411_TYPE 316 SS 37 DEGREE FLARED TUBE FITTING.SLDPRT, 5395T212_SET SCREW RIGID SHAFT COUPLING.SLDPRT, 91251A243_BLACK-OXIDE ALLOY S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]
2017-04-06 adding old v1-v3 EFS solidworks drawings
    [1_8 OD tubing fitting 50715K411_TYPE 316 SS 37 DEGREE FLARED TUBE FITTING.SLDPRT, 5395T212_SET SCREW RIGID SHAFT COUPLING.SLDPRT, 91251A243_BLACK-OXIDE ALLOY S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]
2017-04-06 add 8kN exploration and some file structure changes
    [1_8 OD tubing fitting 50715K411_TYPE 316 SS 37 DEGREE FLARED TUBE FITTING.SLDPRT, 5395T212_SET SCREW RIGID SHAFT COUPLING.SLDPRT, 91251A243_BLACK-OXIDE ALLOY S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]
2017-04-07 adding impellers for fabrication 1
    [PSU_EFS_impeller_3A_test_4_6_17.STL, impeller_1_for_DMLS_JL_4_1_17.SLDPRT]
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2017-04-07 Revert "Moved CAD folder"
    This reverts commit 8f10c33e93369aa0595cd2fe8d1178060e3675e4.
    [1_8 OD tubing fitting 50715K411_TYPE 316 SS 37 DEGREE FLARED TUBE FITTING.SLDPRT, 5395T212_SET SCREW RIGID SHAFT COUPLING.SLDPRT, 91251A243_BLACK-OXIDE ALLOY S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]
2017-04-08 adding v5, new impeller logic
    [1_8 OD tubing fitting 50715K411_TYPE 316 SS 37 DEGREE FLARED TUBE FITTING.SLDPRT, 5395T212_SET SCREW RIGID SHAFT COUPLING.SLDPRT, 91251A243_BLACK-OXIDE ALLOY S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]
2017-04-08 adding updates to v5, still incomplete
    [9452K161_OIL-RESISTANT BUNA-N MULTIPURPOSE O-RING.SLDPRT, EFS_v5_assembly.SLDASM, big_seal_JL_3_14_17.SLDPRT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]
2017-04-11 adding impellers for fabrication
    [EFS_v5_assembly.SLDASM, housing_v5.SLDPRT, housing_v5_B.SLDPRT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]
2017-04-11 adding STL files for impellers
    [impeller_v5_for_fab_1A_6_vane.STL, impeller_v5_for_fab_2A_8_vane.STL, impeller_v5_for_fab_3A_10_vane.STL]
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2017-04-12 Add BOM to documentation
    [BOM.xlsx]
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2017-04-12 Moved active BOM to purchasing folder
    [Active BOM.xlsx]
2017-04-12 Another CAD file structure fix
    [impeller_v5_for_fab_3A_10_vane.SLDPRT, impeller_v5_for_fab_3A_10_vane.STL]
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2017-04-12 just some v5 changes
    [EFS_v5_assembly.SLDASM, housing_v5_B.SLDPRT]
2017-04-13 bearing system and shaft
    [Locating Bearing Plate.SLDPRT, Nonlocating Bearing Plate.SLDPRT, Shaft_Bearing System.SLDPRT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]
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2017-04-13 adding small v5 stuff including o ring for jordan
    [10_degree_diffuser.SLDPRT, 12_degree_diffuser.SLDPRT, 8_degree_diffuser.SLDPRT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]
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2017-04-15 Fixed V5 impeller houseing thin wall failure. Added STL go file.
    [housing_v5_interchangeable_diffuser - for DMLS.SLDPRT, housing_v5_interchangeable_diffuser - for DMLS.STL]
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2017-04-17 CAD file structure fix
    [lower seal plate v6.SLDPRT]
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2017-04-18 trying to add v6 housing with mount flanges
    [housing_v6_CNC_with mount.SLDPRT]
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2017-04-19 updating motor mounts and housing and flanges and.... (v6)
    [12_degree_diffuser.SLDPRT, 9452K240_OIL-RESISTANT BUNA-N MULTIPURPOSE O-RING.SLDPRT, diffuser flange.SLDPRT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]
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2017-04-20 correct titleblocks for drawings
    [20mm Nonlocating Bearing Plate.SLDDRW, Locating Bearing Plate v6.SLDDRW, lower seal plate v6.SLDDRW]
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2017-04-21 add boring bar to be ordered to BOM
    [Active BOM.xlsx]
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2017-04-21 fix diffuser blank
    [diffuser_blank.SLDPRT, diffuser_blank.STL]
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2017-04-27 Added plumbing cad files and updated fittings spec
    [4067T310_BRASS BALL VALVE W COMPRESSION TUBE FITTING.SLDPRT, 50785K228_MED-PRESSURE BRASS THREADED PIPE FITTING.SLDPRT, 50785K240_MED-PRESSURE BRASS THREADED P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]
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2017-04-28 Updated fittings oder and added raw stock to active BOM
    [Active BOM.xlsx, Fittings_level_tmp.xlsx]
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2017-04-29 Massive integration of fittings order into active BOM
    [Active BOM.xlsx, Fittings_level_tmp.xlsx]
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2017-04-30 Edits to EFS_BOM and file structure fixes
    [10_degree_diffuser.SLDPRT, 10_degree_diffuser.STL, 12_degree_diffuser.SLDDRW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]
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2017-06-01 Removed LFETS reference BOM, no longer needed
    [LFETS_copy.xlsx]
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2017-06-03 Complete plot script, still needs to be automated for incoming data
    [17500.csv]
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2017-06-10 cleanup and finish BOM BOM_tmp is complete EFS_BOM contains product breakdown
    [EFS_BOM_tmp.xls]
2017-06-10 fix file type
    [EFS_BOM_tmp.xls, EFS_BOM_tmp.xlsx]
2017-06-10 fix accounting error
    [EFS_BOM_tmp.xlsx]
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2017-06-14 BOM edits. Please use only one BOM! Use EFS_BOM for recording purchases.
    [EFS_BOM.xlsx]
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
